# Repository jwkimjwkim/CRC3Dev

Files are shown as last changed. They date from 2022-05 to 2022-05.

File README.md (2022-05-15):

# CRC3Dev
Tracking Development of CRC3 Quadrotor Biplane Tailsitter

Important Files:

CRC3 Documentation.docx: All documentation of processes carried out in the process of building the drone and handling the firmware, QGroundControl, etc.

CRC mini_VTOL_UMD_BOM.xlsx: Bill of Materials, make sure you are on the "New BOM" tab. The "Old BOM" tab is what was given to us by ARL.

ISAaC CRC3 Presentation.ppt: ppt presentation given by Anton, Jacob, and Trenton at the end of Spring 2022 semester

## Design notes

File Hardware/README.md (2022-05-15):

Add Hardware related files here. Add subrepositories as necessary

CRC3.sldprt: Original solidworks file of full drone assembly received from ARL
CRC3.x_t: Parasolid of above .sldprt file

Body_Assembly.prt: Assembly of modified body and inner components
CRC3_sldprt.prt: NX file of full CRC3 assembly
NOTE: Any file titled "Body_#" is a converted NX part file corresponding to the full assembly NX file. To figure out which part it references, see the assembly list within the assembly file.

Any .stl files are exactly as 3D printed

WingSpar.dxf: file used to laser cut balsa wood spar

WingXSolid.dxf: file used to laser cut airfoil cross section

SupportBoard.dxf: file used to laser cut balsa wood support struts that run perpendicular to the wings. NOTE: I recommend measuring the gap on the drone itself and sizing this part according to how you want everything spaced.

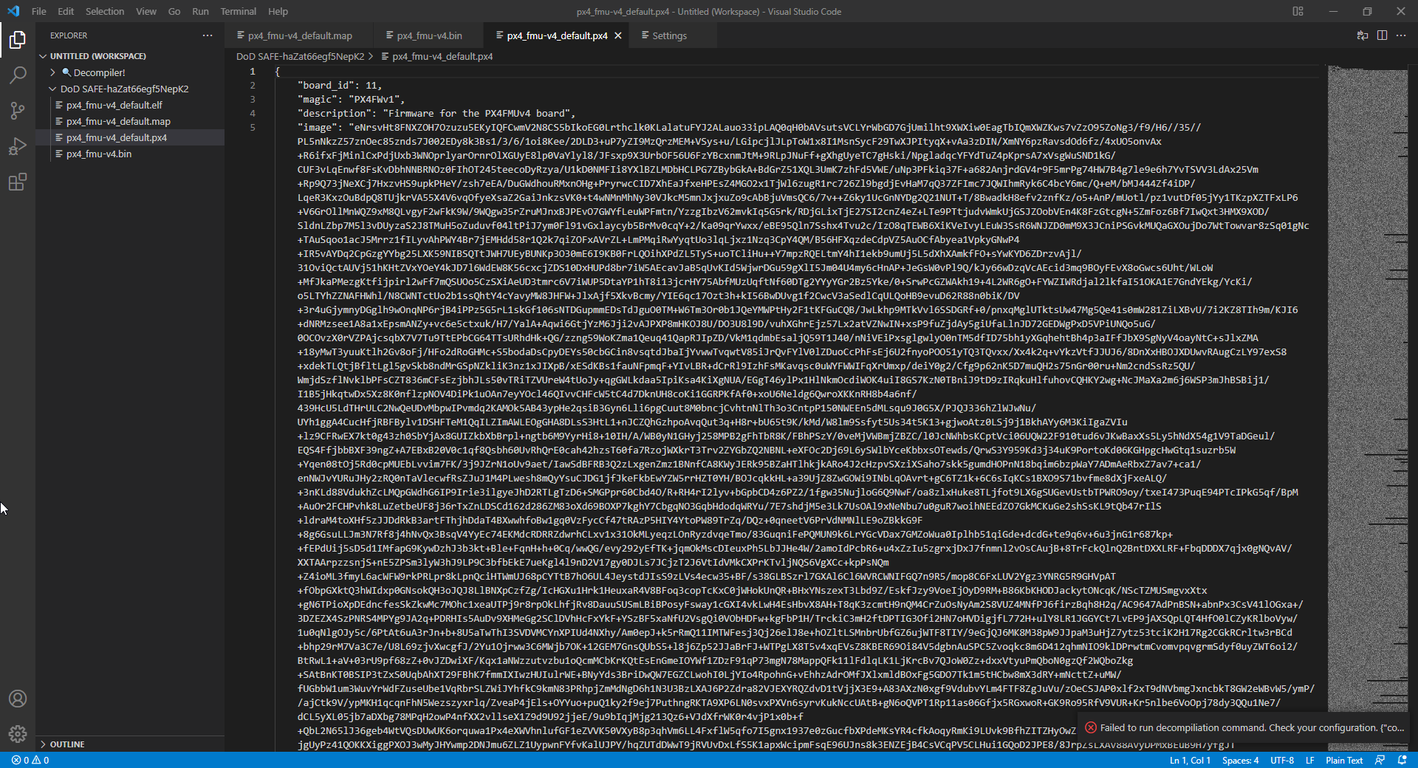
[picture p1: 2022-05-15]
Software/HeaderOfFirmwarePX4Files.png

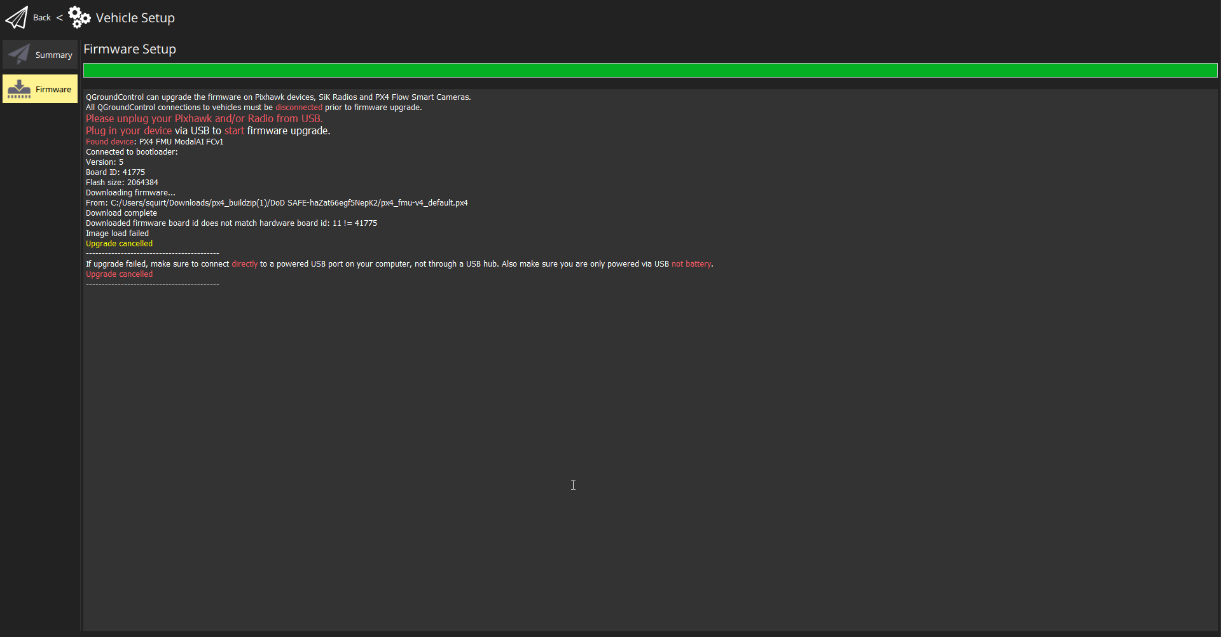
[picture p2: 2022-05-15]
Software/FirmwareUploadError.png

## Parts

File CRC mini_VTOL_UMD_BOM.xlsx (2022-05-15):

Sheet: Old BOM
part | part number | supplier | qty | price | extended price | notes | status | link
Motors |  | rctimer | 4 | 14.99 | 59.96 | Need motor specs to find a replacement | Unavailable | http://rctimer.com/?product-813.html
ESC pack of 4 |  | Amazon | 1 | 42.99 | 42.99 |  | Unavailable | https://www.amazon.com/gp/product/B07FD4G32J/ref=ppx_yo_dt_b_asin_title_o01__o00_s00?ie=UTF8&psc=1
prop 8x6 |  | Amazon | 1 | 8.99 | 8.99 | 8x6? Link says 8x4.5 | Unavailable | https://www.amazon.com/gp/product/B06XKWJTPL/ref=ppx_yo_dt_b_asin_title_o00__o00_s00?ie=UTF8&psc=1
Carbon Tube .25" | 46400-G-DL | Rock West | 1 | 24.99 | 24.99
3/16" aircraft ply for center plate |  | obby Hangar | 1 | 10 | 10 | Size? | Not Found | Purchased locally
Silicone wire |  | Amazon | 2 | 6.98 | 13.96 |  | Not Found | https://www.amazon.com/BNTECHGO-Silicone-Flexible-Strands-Stranded/dp/B01AQOI36M
White Monokote |  | Tower Hobbies | 1 | 14.99 | 14.99 |  | Not Found | https://www.towerhobbies.com/cgi-bin/wti0001p?I=TOPQ0204&P=FR
Yellow monokote |  | Tower Hobbies | 1 | 14.99 | 14.99 |  |  | https://www.towerhobbies.com/cgi-bin/wti0001p?&I=LXHV38&P=ML
Black Trim Tape |  | Horizon Hobby | 1 | 9.99 | 9.99 |  |  | https://www.horizonhobby.com/ultrastripe--black-3-32-hanu80430
Foam Wing core |  | MOHR |  |  | 0 |  |  | Custom made
MDF for mold |  | Home Depot | 1 | 10 | 10 |  |  | Bought at store
fiberglass 3/4oz |  | Tower Hobbies | 1 | 9.99 | 9.99 |  | Not Found | https://www.towerhobbies.com/cgi-bin/wti0001p?&I=LXL491&P=ML
fiberglass 4oz |  | Tower Hobbies | 1 | 9.99 | 9.99 |  | Not Found | https://www.towerhobbies.com/cgi-bin/wti0001p?&I=LXL493&P=7
Breather cloth | V351 | CST Sales | 1 | 8.35 | 8.35
Peel ply | V287 | CST Sales | 1 | 10.45 | 10.45
vacuum tape | V196 | CST Sales | 1 | 10.45 | 10.45
Vacuum bag | V121 | CST Sales | 1 | 11.81 | 11.81
PV mold release |  | Amazon | 1 | 25 | 25 |  |  | https://www.ebay.com/i/372197648276?chn=ps
3x22mm screw |  | McMaster | 1 | 11 | 11 | pack of 100 |  | https://www.mcmaster.com/91290a124
3x10mm screw |  | McMaster |  |  | 0 |  |  | https://www.mcmaster.com/91290a115
3mm nut |  | McMaster |  |  | 0 |  |  | https://www.mcmaster.com/90576a102
3x14mm screw |  | McMaster |  |  | 0 |  |  | https://www.mcmaster.com/91290a119
3x8mm screw |  | McMaster |  |  | 0 |  |  | https://www.mcmaster.com/91290a113
Balsa sheeting for wings | 63 | Balsa USA | 6 | 1.18 | 7.08
West Systems Epoxy 105/205 |  | Amazon | 1 | 74.95 | 74.95 |  |  | https://www.amazon.com/dp/B07JGJ84Y4

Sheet: New BOM
part | part number | supplier | qty | price | extended price | notes | link
Motors and Props |  | Amazon | 1 | 66.99 | 66.99 |  | https://www.amazon.com/gp/product/B07D9367RZ/ref=ox_sc_saved_title_1?smid=A2QTZX14X1D97I&psc=1
ESC pack of 4 |  | Amazon | 1 | 56.95 | 56.95 |  | https://www.amazon.com/RacerStar-Brushless-MultiShot-BLHeli-RS30A/dp/B076MYSGJL
fiberglass 3/4oz |  | Amazon | 1 | 25.95 | 25.95 |  | https://www.amazon.com/Fiberglass-Cloth-0-75-Yards-Folded/dp/B07X4CGFP1
fiberglass 4oz |  | Amazon | 1 | 14.95 | 14.95 |  | https://www.amazon.com/Fiberglass-Cloth-Yard-Pack-12-5/dp/B07SM2RZCB
West Systems Epoxy 105/205 |  | Amazon | 1 | 76.47 | 76.47 |  | https://www.amazon.com/dp/B07JGJ84Y4
Peel ply | V287 | CST, The Composite Store | 1 | 13.5 | 13.5 |  | https://www.cstsales.com/shop-bin/sc/productsearch.cgi?storeid=*14894f2aabc441e61a44715a
vacuum tape | V196 | CST, The Composite Store | 1 | 11.3 | 11.3 |  | https://www.cstsales.com/shop-bin/sc/productsearch.cgi?storeid=*14894f2aabc441e61a44715a
Vacuum bag | V121 | CST, The Composite Store | 1 | 11.8 | 11.8 |  | https://www.cstsales.com/shop-bin/sc/productsearch.cgi?storeid=*14894f2aabc441e61a44715a
PV mold release |  | Fibreglast | 1 | 10.75 | 10.75 | 1 Quart; Previously purchased on ebay Used for releasing parts from mold. Didn't end up using it | https://www.fibreglast.com/product/PVA_Release_Film_13/Mold_Releases
3x22mm screw |  | McMaster | 1 | 11 | 11 | pack of 100 | https://www.mcmaster.com/91290a124
3x10mm screw |  | McMaster | 1 | 8.4 | 8.4 | pack of 100 | https://www.mcmaster.com/91290a115
3mm nut |  | McMaster | 1 | 3.82 | 3.82 | pack of 100 | https://www.mcmaster.com/90576A102/
3x14mm screw |  | McMaster | 1 | 12.67 | 12.67 | pack of 100 | https://www.mcmaster.com/91290a119
3x8mm screw | 95263A122 | McMaster | 1 | 8.12 | 8.12 | pack of 50 | https://www.mcmaster.com/catalog/127/3357/
Silicone wire |  | Home Depot |  |  |  | Gauge?
White Monokote | TOPQ0204 | Tower Hobbies | 1 | 16.99 | 16.99 | Surface area needed? | https://www.towerhobbies.com/product/monokote-jet-white-6/TOPQ0204.html
Yellow monokote | TOPQ0220 | Tower Hobbies | 1 | 15.29 | 15.29 | Surface area needed? | https://www.towerhobbies.com/product/monokote-cub-yellow-6/TOPQ0220.html
Carbon Tube .25" | 46400-G-DL | Rock West | 1 | 45.99 | 45.99 | 74" total | https://www.rockwestcomposites.com/46400-g-dl
PLA Filament |  |  | 2 | 24.83 | 49.66 | Printing material for bracketing | https://www.amazon.com/gp/product/B01EKEMDA6/ref=ppx_yo_dt_b_asin_title_o00_s00?ie=UTF8&th=1
12 Gauge Silicone Wire |  | Amazon | 1 | 7.48 | 7.48 |  | https://www.amazon.com/BNTECHGO-Silicone-Flexible-Strands-Stranded/dp/B01AQU3ST8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
18 Guage Silicone Wire |  | Amazon | 1 | 6.98 | 6.98 |  | https://www.amazon.com/BNTECHGO-Silicone-Flexible-Strands-Stranded/dp/B01708AYYQ
Servo Extension Cable Wire |  | Amazon | 1 | 10.99 | 10.99 |  | https://www.amazon.com/TecUnite-Extension-Connectors-Connection-Control/dp/B07C18BXDV?psc
XT60 Connector |  | Amazon | 1 | 9.99 | 9.99 |  | https://www.amazon.com/Amass-Bullet-Connector-Upgrated-Sheath/dp/B074PN6N4K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
Heat Shrink Tubing |  | Amazon | 1 | 9.89 | 9.89 |  | https://www.amazon.com/650pcs-Shrink-Tubing-innhom-Approved/dp/B07WWWPR2X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
3.5 mm Bullet Connectors |  | Amazon | 1 | 13.69 | 13.69 |  | https://www.amazon.com/ShareGoo-Female-Banana-Connector-Battery/dp/B00EZLNZV6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
Foam Wing core |  |  | 2 | 40 | 80 | Custom? Need wing core specs
RC Receiver |  |  | 1 | 33.99 | 33.99 |  | https://www.getfpv.com/frsky-rx6r-2-4g-receiver.html
RC Transmitter |  | Amazon | 1 | 136.99 | 136.99 |  | https://www.getfpv.com/frsky-x9-lite-s-access-2-4g-24ch-radio-transmitter.html
LiPo Battery |  |  | 1 | 28.49 | 28.49 |  | https://www.amazon.com/gp/product/B08KD1YN9F/ref=ppx_yo_dt_b_asin_title_o00_s00?ie=UTF8&psc=1
LiPo Charger |  |  | 1 | 11.99 | 11.99 |  | https://www.amazon.com/gp/product/B072K5LHGM/ref=ppx_yo_dt_b_asin_title_o00_s00?ie=UTF8&psc=1
Temporary Airframe |  | Amazon | 1 | 21.99 | 21.99 | For testing of electronics/software for hover | https://www.amazon.com/gp/product/B07H3WDSX3/ref=ppx_yo_dt_b_asin_title_o00_s00?ie=UTF8&psc=1
Power Distribution Board |  | getfpv.com | 1 | 16.18 | 16.18
Fireproof Battery Case |  | Amazon | 1 | 10.99 | 10.99 |  | https://www.amazon.com/gp/product/B01GCHBQJS/ref=ppx_yo_dt_b_asin_title_o00_s00?ie=UTF8&psc=1
LIPO Charger |  | Amazon | 1 | 149.9 | 149.9 |  | https://www.amazon.com/gp/product/B07L3LVCQR/ref=ppx_yo_dt_b_asin_title_o00_s00?ie=UTF8&psc=1
Foam Wings |  | Matney Models | 2 | 40 | 80 |  | http://www.matneymodels.com/index.html
1/16" Balsa Wood |  | RPI Bookstore | 1 | 7 | 7 | Support Struts
1/8" Balsa Wood |  | RPI Bookstore | 1 | 7 | 7 | Wing Spar
RC connector |  | modalAI | 1 | 14.98 | 14.98 |  | https://www.modalai.com/products/rc-input-cable-servo-s-bus-frsky
 |  |  |  | TOTAL | 1119.12

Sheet: Measurements
Carbon Tube # (according to Part Name in CRC3.prt) | Length (mm)
5 | 137
7 | 130
14 | 137
21 | 156.8026
22 | 156.8026
23 | 137
24 | 137
32 | 130
37 | 130
39 | 130
49 | 151.8026
50 | 156.8026

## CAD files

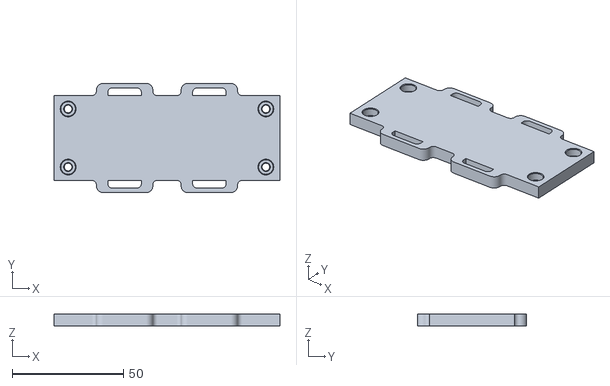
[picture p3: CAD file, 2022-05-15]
Hardware/CAD/Battery_plate.stl
101.6 x 49.1 x 5.50

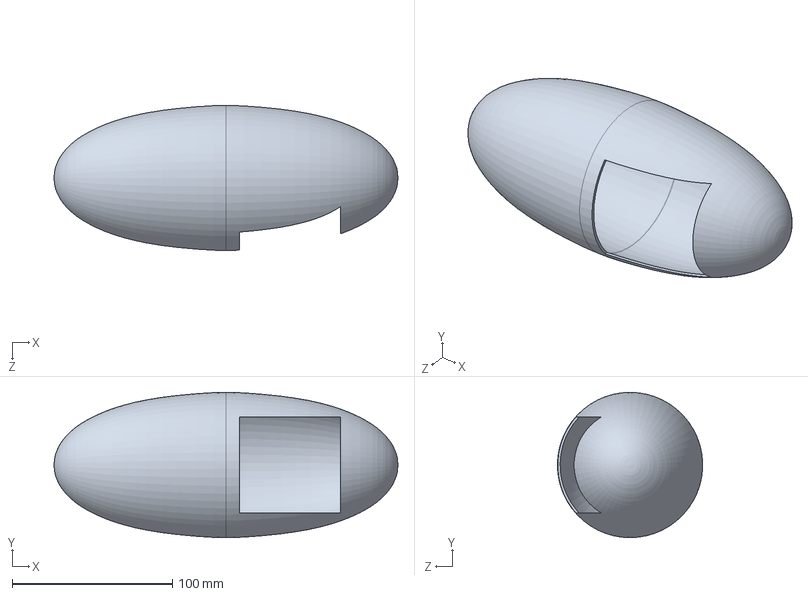
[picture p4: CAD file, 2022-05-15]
Hardware/CAD/Body.SLDPRT
214.7 x 90.7 x 90.6 mm

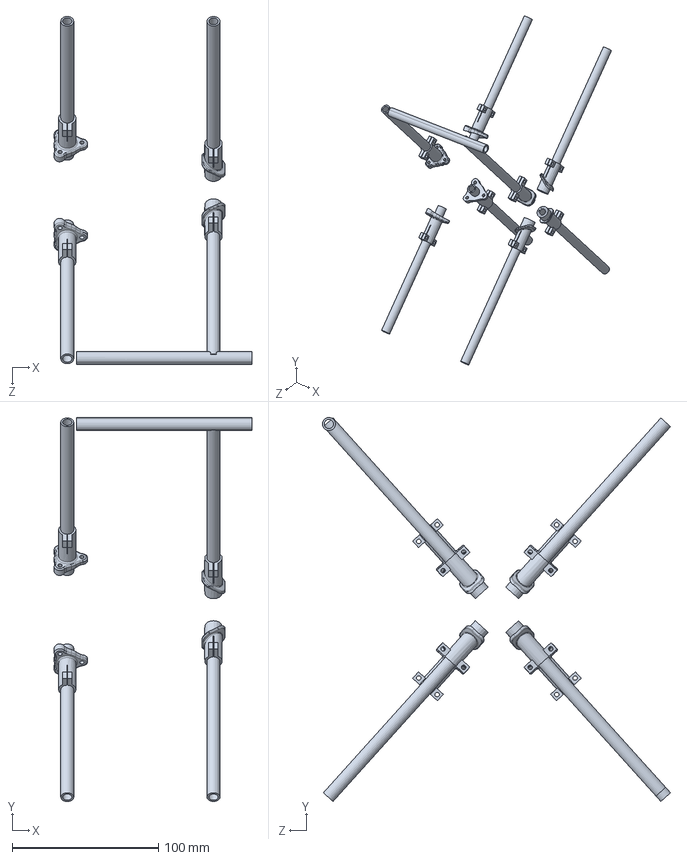
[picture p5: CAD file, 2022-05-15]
Hardware/CAD/Brackets.SLDPRT
135.3 x 262.6 x 238.1 mm

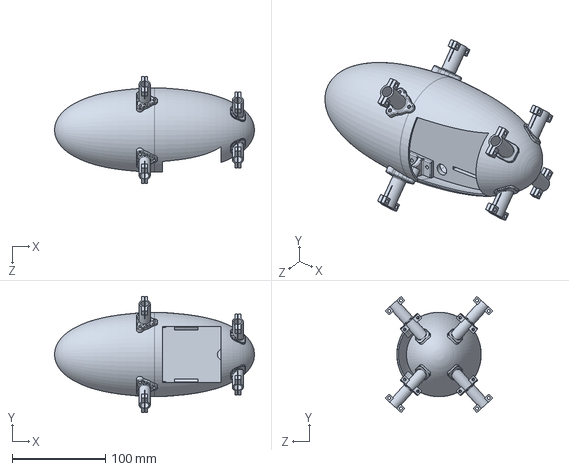
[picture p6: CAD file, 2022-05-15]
Hardware/CAD/Body_wBrackets.SLDPRT
214.7 x 124.6 x 115.4 mm

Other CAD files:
Hardware/CAD/Battery.prt
Hardware/CAD/Battery_plate.prt
Hardware/CAD/Body.STL
Hardware/CAD/Body.prt
Hardware/CAD/Body.x_t
Hardware/CAD/Body_10_sldprt.prt
Hardware/CAD/Body_11_sldprt.prt
Hardware/CAD/Body_12_sldprt.prt
Hardware/CAD/Body_13_sldprt.prt
Hardware/CAD/Body_14_sldprt.prt
Hardware/CAD/Body_15_sldprt.prt
Hardware/CAD/Body_16_sldprt.prt
Hardware/CAD/Body_17_sldprt.prt
Hardware/CAD/Body_18_sldprt.prt
Hardware/CAD/Body_19_sldprt.prt
Hardware/CAD/Body_20_sldprt.prt
Hardware/CAD/Body_21_sldprt.prt
Hardware/CAD/Body_22_sldprt.prt
Hardware/CAD/Body_23_sldprt.prt
Hardware/CAD/Body_24_sldprt.prt
Hardware/CAD/Body_25_sldprt.prt
Hardware/CAD/Body_26_sldprt.prt
Hardware/CAD/Body_27_sldprt.prt
Hardware/CAD/Body_28_sldprt.prt
Hardware/CAD/Body_29_sldprt.prt
Hardware/CAD/Body_2_sldprt.prt
Hardware/CAD/Body_30_sldprt.prt
Hardware/CAD/Body_31_sldprt.prt
Hardware/CAD/Body_32_sldprt.prt
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

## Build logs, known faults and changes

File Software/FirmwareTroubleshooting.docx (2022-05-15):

Looks like they used a Pixhawk board with FMUv4 architecture (possibly pixracer)

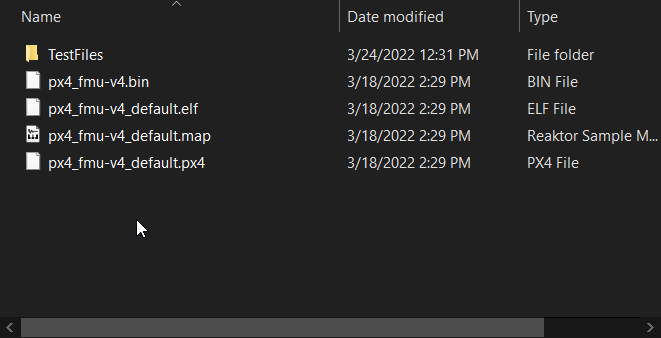
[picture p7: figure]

The flight core says

- “ModalAI Flight Core is a PX4 flight controller that uses a very similar architecture to FMUv5x. It’s design goal is to be software compatible with the FMUv5x architecture in a smaller Pixracer-style form factor.”
- https://docs.modalai.com/flight-core-datasheets-functional-description/

So in my understanding, we are trying to flash firmware meant for an FMUv4 architecture onto an FMUv5 board.

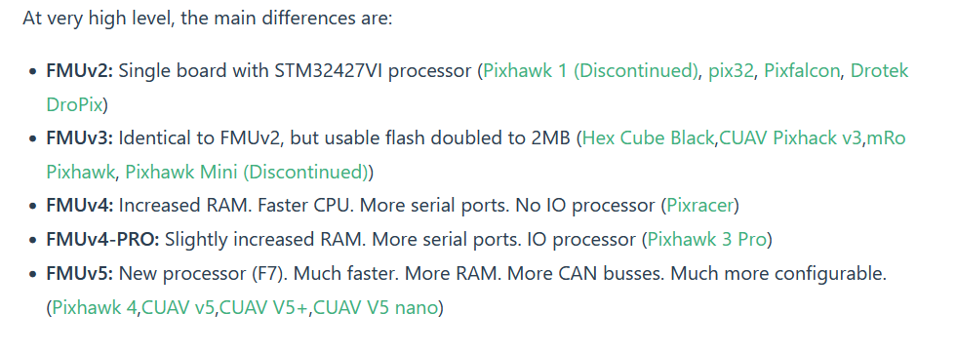
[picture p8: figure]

Source: https://docs.px4.io/v1.12/en/flight_controller/pixhawk_series.html

Apparently the FMU standard says the boards of the same FMU version should be compatible across different boards built on it:

FOR REFERENCE: this is the current firmware on the board:

https://docs.modalai.com/flight-core-firmware/

We were able to change the board id of the DOD firmware to the right number (41775, was 11 previously) manually. The firmware successfully flashed, but upon restart, the flight core gets stuck in its bootloader, indicated by 10 Hz flashing green light. Through a quick internet search, we determined that this was due to incompatible firmware.

- Source: https://www.racedayquads.com/tools/forum/forums/4792-tech-help-problem-solving/topics/17025-flash-latest-beta-flight-then-fc-stuck-in-boot

Luckily, the chip inside the flight core is impossible to brick, as per this source

- Source: https://docs.px4.io/master/en/advanced_config/bootloader_update_from_betaflight.html

Some parameters of the DOD firmware are shown below

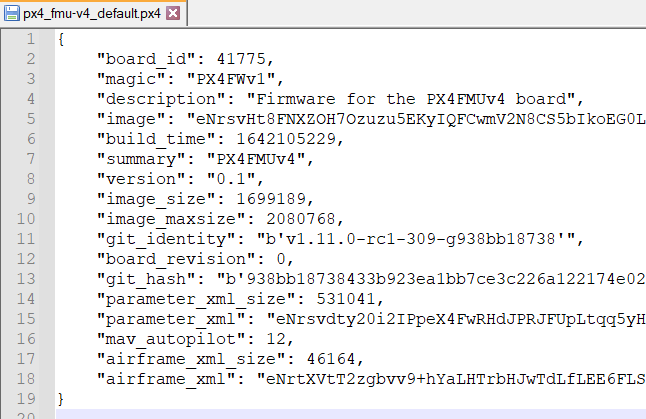
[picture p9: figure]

of note is git_identity - could maybe show where they forked from??

You can also see where the board_id is checked
